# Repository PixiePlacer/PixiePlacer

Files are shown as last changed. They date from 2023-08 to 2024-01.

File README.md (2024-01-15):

# PixiePlacer
Welcome OpenPnP Community to the **PixiePlacer Wiki**!
The PixiePlacer is a **DIY Pick and Place Machine** for SMD Components based around the amazing software **[OpenPnP](https://openpnp.org)**. The machine is designed to be low cost and suited towards mid-scale manufacturing. A big shout out to the developers of [OpenPnP](https://openpnp.org) that keep constantly improving the software.



Something looks wrong? Please [let me know](https://github.com/PixiePlacer/PixiePlacer/issues/new)!

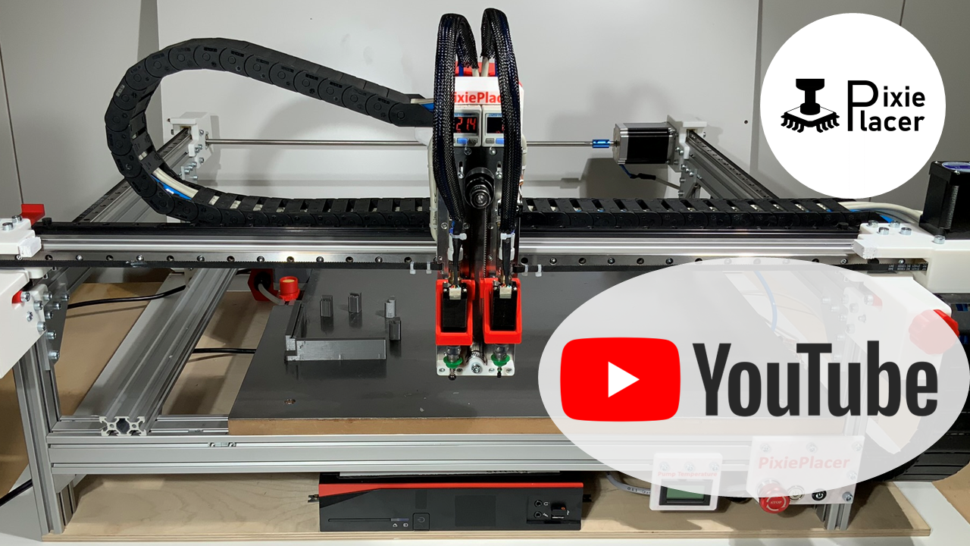
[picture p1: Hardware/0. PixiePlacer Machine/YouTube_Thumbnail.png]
PixiePlacer (https://www.youtube.com/@pixieplacer)


# PixiePlacer Machine
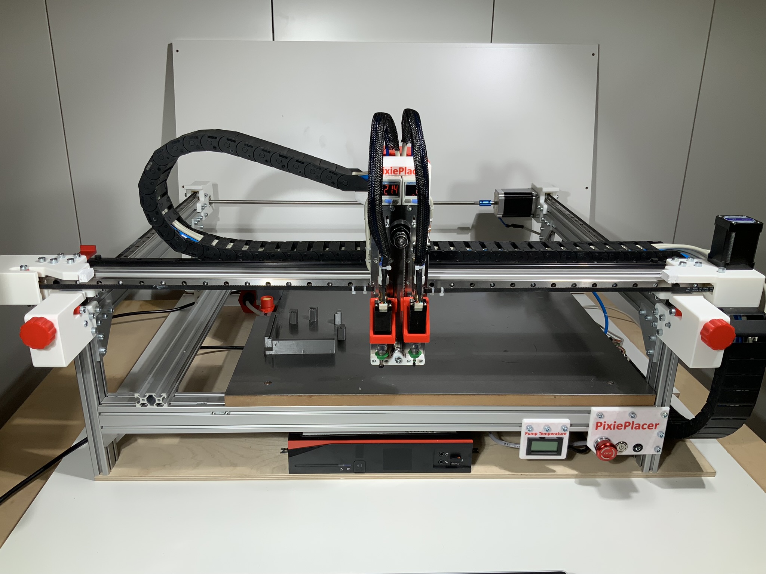
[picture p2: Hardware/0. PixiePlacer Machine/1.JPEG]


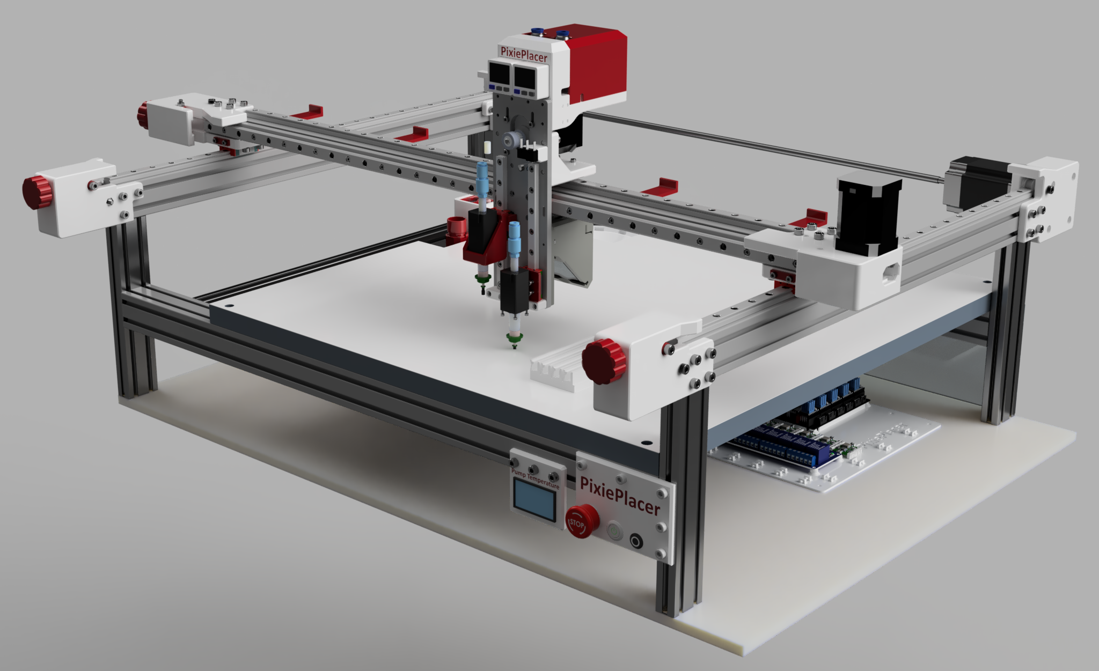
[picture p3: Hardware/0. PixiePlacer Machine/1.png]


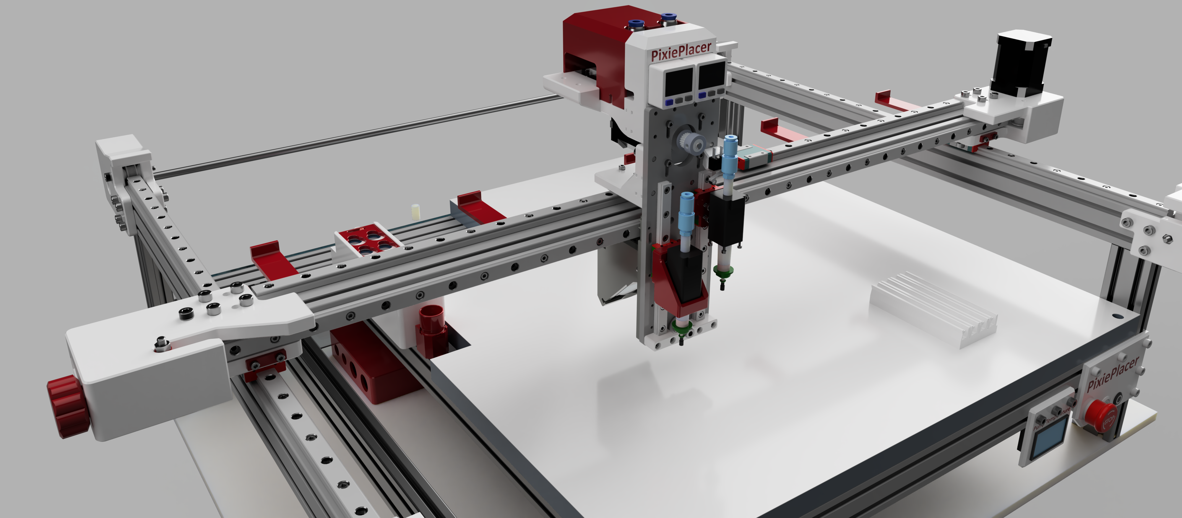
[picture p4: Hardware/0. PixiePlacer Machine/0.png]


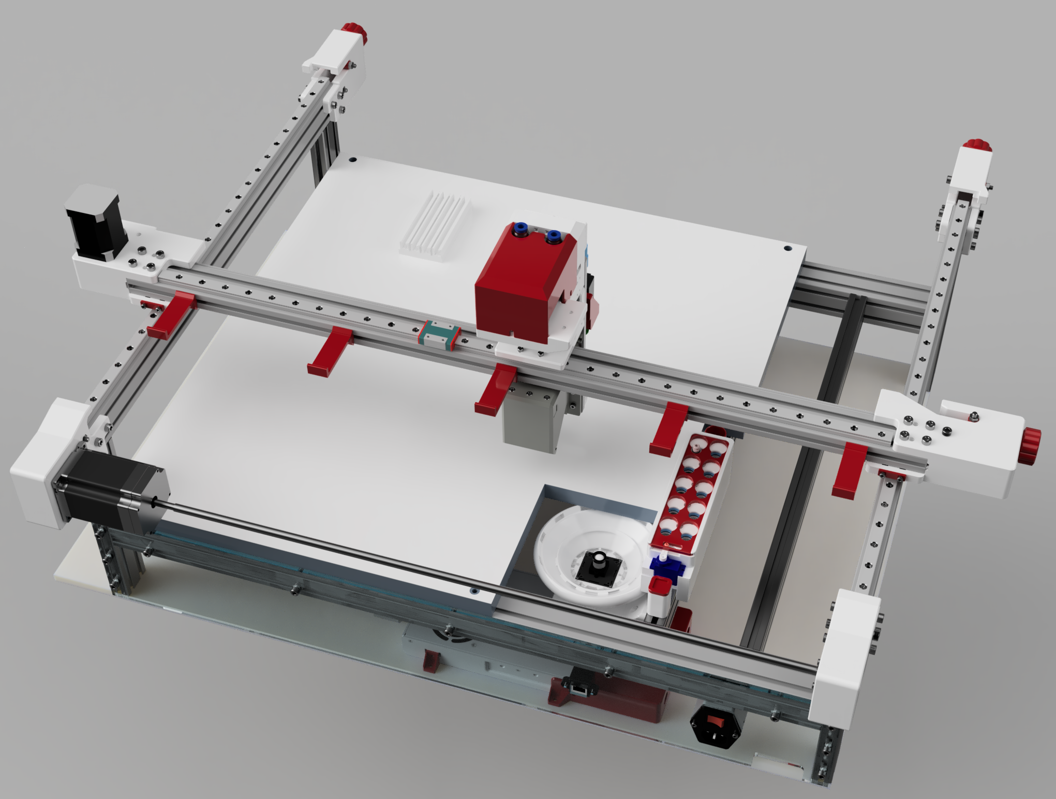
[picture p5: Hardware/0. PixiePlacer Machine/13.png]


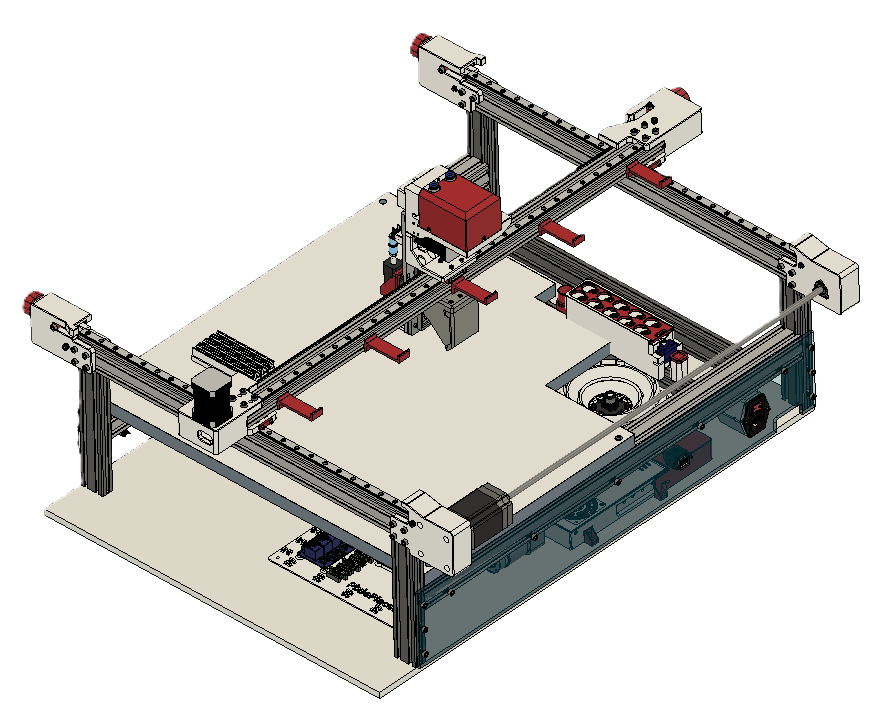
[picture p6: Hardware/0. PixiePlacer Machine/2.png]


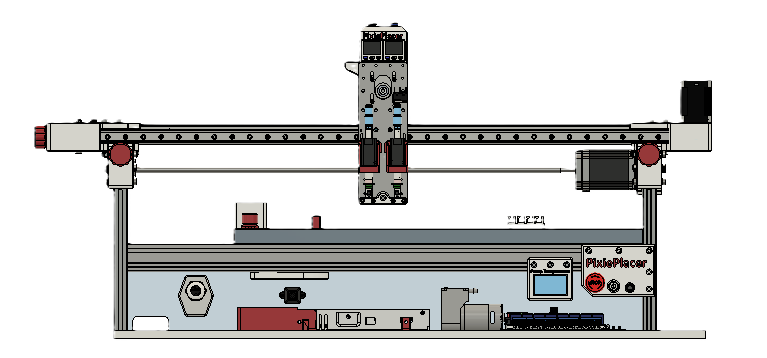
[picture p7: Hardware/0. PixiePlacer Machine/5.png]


***
# Overview
 - [Overview](https://github.com/PixiePlacer/PixiePlacer/wiki/Overview)

# Bill of Materials | BOM
 - [Bill of Materials](https://github.com/PixiePlacer/PixiePlacer/wiki/Bill-of-Materials)
 
# Hardware
 - [Machine Frame](https://github.com/PixiePlacer/PixiePlacer/wiki/Machine-Frame)
 - [Y‐Axis](https://github.com/PixiePlacer/PixiePlacer/wiki/Y%E2%80%90Axis)
 - [X‐Axis](https://github.com/PixiePlacer/PixiePlacer/wiki/X%E2%80%90Axis)
 - [Z‐Axis](https://github.com/PixiePlacer/PixiePlacer/wiki/Z%E2%80%90Axis)
 - Accessories
	- [PCB Holder](https://github.com/PixiePlacer/PixiePlacer/wiki/PCB-Holder)
	- [Down Facing Camera](https://github.com/PixiePlacer/PixiePlacer/wiki/Down-Facing-Camera)
	- [Up Facing Camera](https://github.com/PixiePlacer/PixiePlacer/wiki/Up-Facing-Camera)
	- [Nozzle Changing Station](https://github.com/PixiePlacer/PixiePlacer/wiki/Nozzle-Changing-Station)
	- [Solderpaste Dispensing](https://github.com/PixiePlacer/PixiePlacer/wiki/Solderpaste-Dispensing)

# Electronics
 - [Electronics Diagram](https://github.com/PixiePlacer/PixiePlacer/wiki/Electronics-Diagram)
 - [Pneumatic Diagram](https://github.com/PixiePlacer/PixiePlacer/wiki/Pneumatic-Diagram)

# Software

 - [Marlin ‐ Motion Controller](https://github.com/PixiePlacer/PixiePlacer/wiki/Marlin-%E2%80%90-Motion-Controller)
 - [OpenPnP](https://github.com/PixiePlacer/PixiePlacer/wiki/OpenPnP)

# Component Feeder

 - [Parametric Strip Feeder](https://github.com/PixiePlacer/PixiePlacer/wiki/Parametric-Strip-Feeder)
 - [Automagic PixieFeeder](https://github.com/PixiePlacer/PixiePlacer/wiki/Automagic-PixieFeeder)

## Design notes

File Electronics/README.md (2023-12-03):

# Wiki Electronics

## Electronics Wiring Diagramm
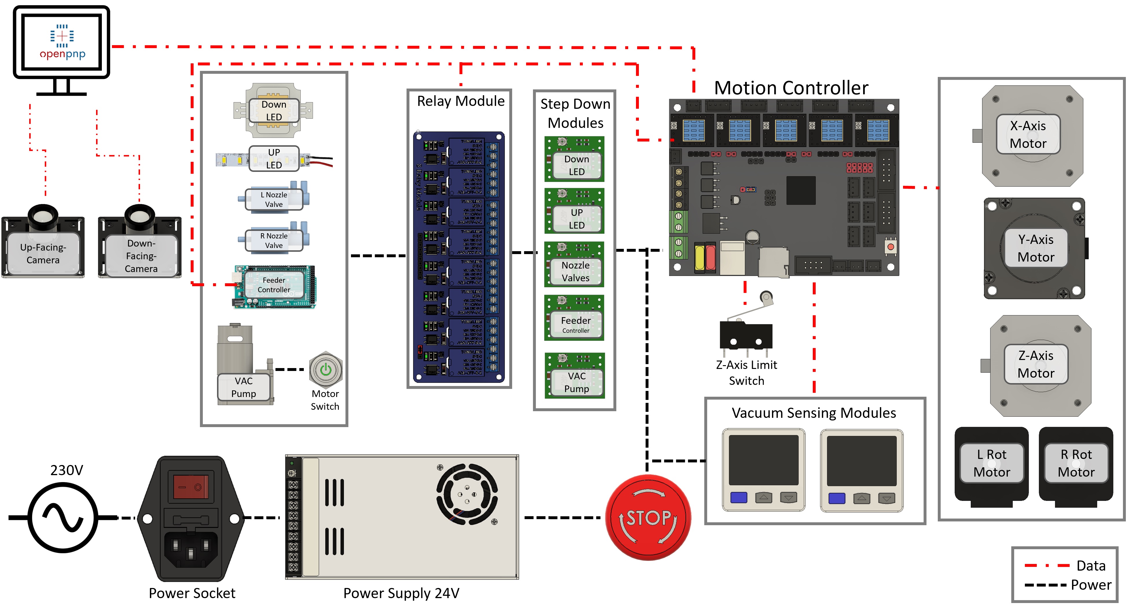
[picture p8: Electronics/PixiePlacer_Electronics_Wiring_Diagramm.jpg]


## Pneuamtic Diagram
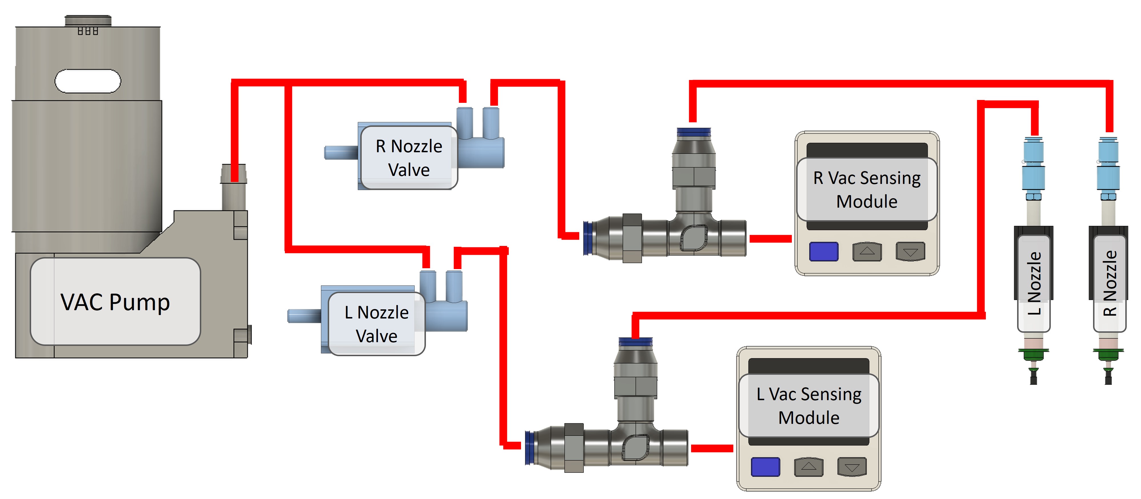
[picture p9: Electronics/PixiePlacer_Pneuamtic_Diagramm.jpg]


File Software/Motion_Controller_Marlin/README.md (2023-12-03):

# [Marlin ‐ Motion Controller Wiki ](https://github.com/PixiePlacer/PixiePlacer/wiki/Marlin-%E2%80%90-Motion-Controller)

**Use the ChangeLog File as a guideline for setting up marlin for your machine.**

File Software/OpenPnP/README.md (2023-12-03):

# [OpenPnP Wiki](https://github.com/PixiePlacer/PixiePlacer/wiki/OpenPnP)

**Use the Machine Setup Files and Driver Setup Files as a guideline for setting up your machine.**

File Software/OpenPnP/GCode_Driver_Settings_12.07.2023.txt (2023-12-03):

++++++++++++  GCode Driver   +++++++++++++
##########  Default  ################

Command Confirm Regrex
	^ok.*

Position Report Regex
	^.*X:(?<X>-?\d+\.\d+) Y:(?<Y>-?\d+\.\d+) Z:(?<Z>-?\d+\.\d+).*

Command Error Regex
	^error.*
	
Connect Command
	G21 ; Set millimeters mode
	G90 ; Set absolute positioning mode
	M82 ; Set absolute mode for extruder
	M42 I M1 P0205 S0; VAC Pump off
	M42 I M1 P0126 S0; LED Top on
	M42 I M1 P0010 S255; LED Bottom off
	M42 I M1 P0100 S255; Air Nozzle 1 off
	M42 I M1 P0125 S255; Air Nozzle 2 off

Disable Command
	M84 ; stepper motor off
	M42 I M1 P0205 S0; VAC off
	M42 I M1 P0205 S0; VAC Pump off
	M42 I M1 P0126 S255; LED Top off
	M42 I M1 P0010 S255; LED Bottom off
	M42 I M1 P0100 S255; Air Nozzle 1 off
	M42 I M1 P0125 S255; Air Nozzle 2 off
	
Home Command
	G28 Z;
	G28 Z;
	G0 Z0 F1000;
	G28 XY
	G0 X0 Y0 Z0 F10000;
	T0 S1;
	G92 E0;
	T1 S1;
	G92 E0;
	M42 I M1 P0205 S0; VAC Pump off
	M42 I M1 P0126 S0; LED Top on
	M42 I M1 P0010 S255; LED Bottom off
	M42 I M1 P0100 S255; Air Nozzle 1 off
	M42 I M1 P0125 S255; Air Nozzle 2 off
	
## Pump On Command
	M42 I M1 P0205 S255; VAC on
	
## Pump Off Command
	M42 I M1 P0205 S0;

Get Position Command
	M114 ; get position
	
Move to Command
	G0 {X:X%.4f} {Y:Y%.4f} {Z:Z%.4f} {Rotation:E%.4f} F{FeedRate:%.0f		
				
Move to Complete Command
	M400 ; Wait for moves to complete before returning

In machine.xml

supporting-pre-move="true" using-letter-variables="false"

<pre-move-command><![CDATA[
					T0S1
					G92E{Coordinate:%.4f}
				]]></pre-move-command>

<pre-move-command><![CDATA[
					T1S1
					G92E{Coordinate:%.4f}
				]]></pre-move-command>		
	
NEW #############   H1 VAC PUMP   #############
Actuate Boolean Command
		{True:M42 I M1 P0205 S255}{False:M42 I M1 P0205 S0}

Not Existing ##############   H1 N1   #####################
Place Command
	M42 I M1 P0100 S255; Air Nozzle 1
	G4 P250;

Not existing ##############   H1 N2   #####################
Place Command
	M42 I M1 P0125 S255; Air Nozzle 2
	G4 P250;

#############   H1 N1_Vac   #############
Actuate Boolean Command
	{True:M42 I M1 P0100 S0}{False:M42 I M1 P0100 S255}
	M42 I M1 P0205 S255; VAC on

#############   H1 N2_Vac   #############
Actuate Boolean Command
	{True:M42 I M1 P0125 S0}{False:M42 I M1 P0125 S255}
	M42 I M1 P0205 S255; VAC on
	
#############   H1 Solder Dispenser   #############
Actuate Boolean Command
	{True:M106 S255}{False:M106 S0}
	
#############   H1 Top Light   #############
Actuate Boolean Command
	{True:M42 I M1 P0010 S255}{False:M42 I M1 P0010 S0}
	{True:M42 I M1 P0126 S0}{False:M42 I M1 P0126 S255}

#############   Bottom Light   #############
Actuate Boolean Command
	{True:M42 I M1 P0010 S0}{False:M42 I M1 P0010 S255}
	{True:M42 I M1 P0126 S255}{False:M42 I M1 P0126 S0}

#############   Shot Solder Dispenser   #############
Actuate Boolean Command
	M106 S255				; On Solder Paste Dispenser
	G4 P500 				; Wait 50ms
	M106 S0					; Off Solder Paste Dispenser

#############   Pneumatic Advance   #############
Actuate Boolean Command
	M106 S0
	G4 P300
	M106 S255

#############   Pneumatic Post Pickup   #############
Actuate Boolean Command

++++++++++++++ Feeder Controller   ++++++++++++++++

##########  Default  ################

Command Confirm Regrex
	^ok.*
	
Command Error Regex
	^error.*	
	
Connect Command
	M610 S1 ; enable feeder

Enable Command
	M610 S1 ; enable feeder

Disable Command
	M610 S0 ; disable feeder
	
#############   Auto Feeder_4mm Advance   #############
Actuate Double Command
	M600 N{IntegerValue} F4
	
#############   Auto Feeder_8mm Advance   #############
Actuate Double Command
	M600 N{IntegerValue} F8

#############   Auto Feeder_12mm Advance   #############
Actuate Double Command
	M600 N{IntegerValue} F12

#############   Auto Feeder_PostPickup   #############
Actuate Double Command
	M601 N{IntegerValue}

#############   Auto Feeder_Enable   #############
Actuate Boolean Command
	M610 S{True:1}{False:0}

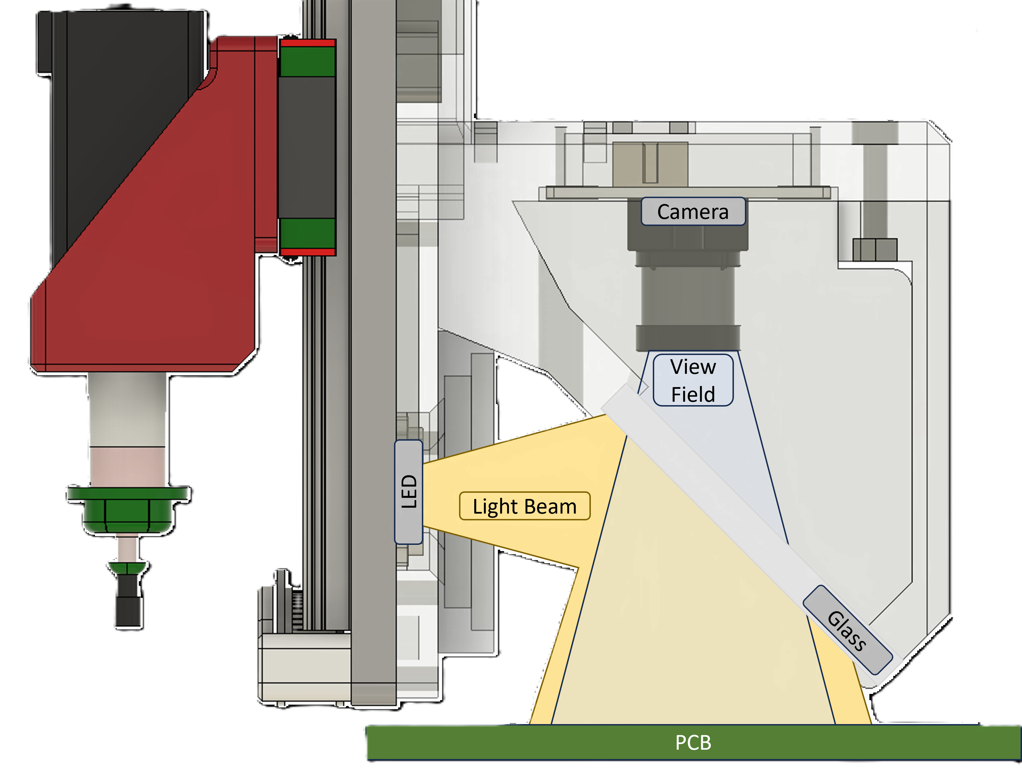
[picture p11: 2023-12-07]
Hardware/5. Accessories/Down-Facing-Camera/Beam-Splitter_Side-View.png

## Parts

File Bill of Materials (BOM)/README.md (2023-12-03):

# Bill of Materials PixiePlacer Table
[Bill of Materials PixiePlacer Table](https://docs.google.com/spreadsheets/d/1CWFQ7bArdYDCNkc-MHFDlqN6pdHpugMOtVum4YUrMk8/edit?usp=sharing)

***

# [Wiki Bill of Materials | BOM](https://github.com/PixiePlacer/PixiePlacer/wiki/Bill-of-Materials)

PixiePlacer (https://www.youtube.com/@pixieplacer)

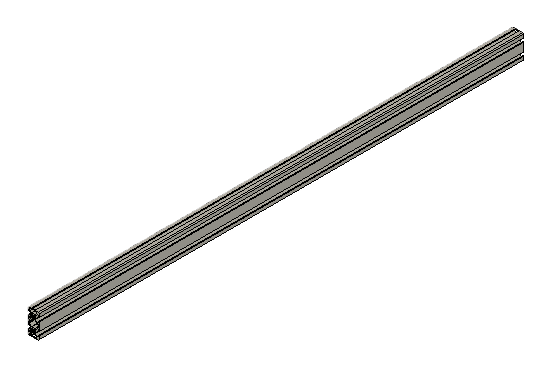
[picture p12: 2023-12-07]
Bill of Materials (BOM)/Parts/3. X-Axis/Alu_Extrusion_X-Axis_798mm.png

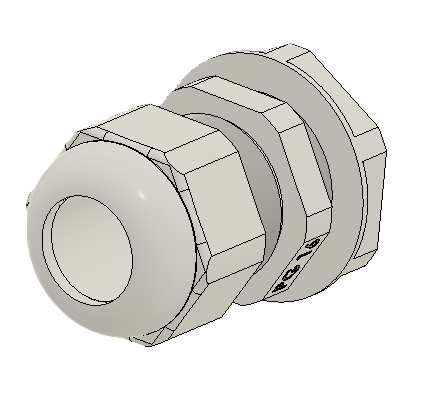
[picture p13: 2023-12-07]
Bill of Materials (BOM)/Parts/1. Machine Frame/Back_Panel/Cable_Gland_PG16.png

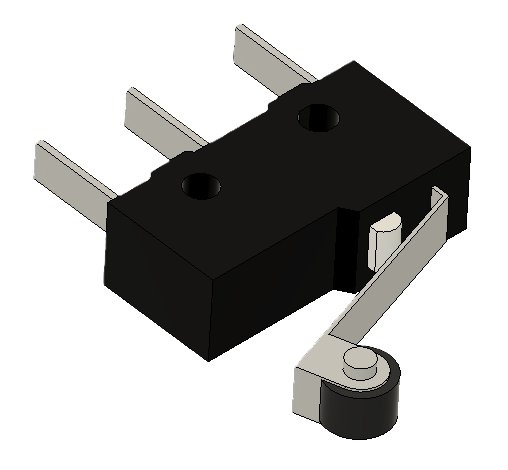
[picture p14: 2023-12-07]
Bill of Materials (BOM)/Parts/4. Z-Axis/Z-Axis_Limit_Switch.png

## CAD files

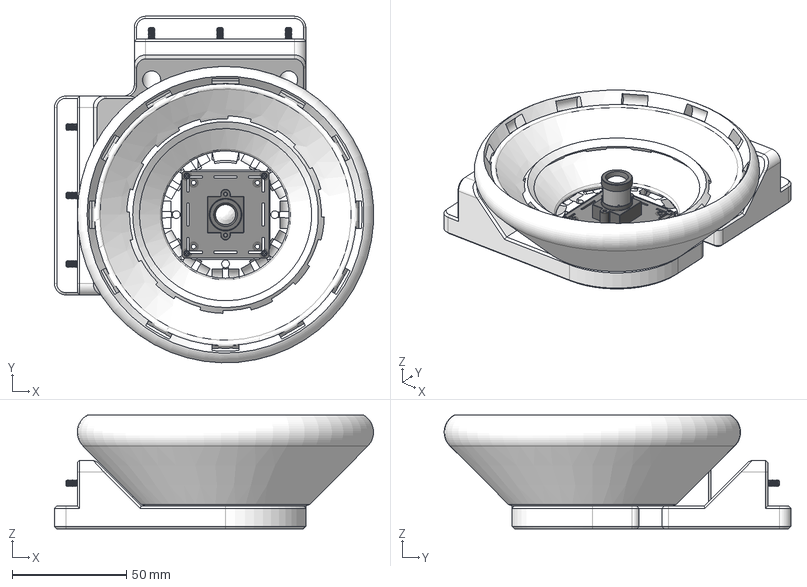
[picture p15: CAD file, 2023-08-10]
Hardware/5. Accessories/Up-Camera/Up_Camera_Assembly.step
139.9 x 152.0 x 49.8 mm
USB_Camera
Socket_Cap_Screw_M3x16mm x 6
99461A913_Phillips Rounded Head Thread-Forming Screws x 4

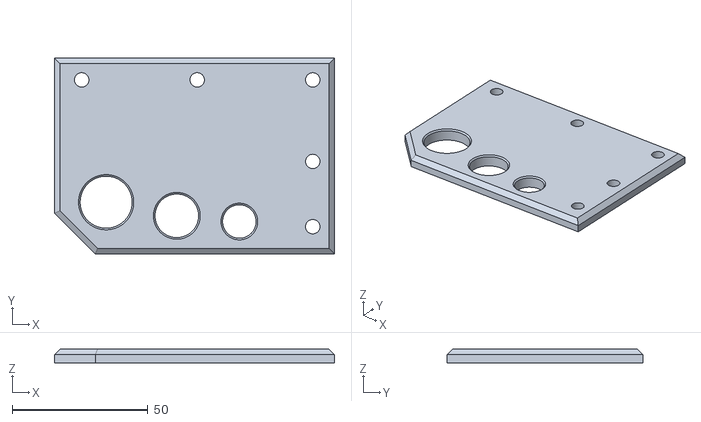
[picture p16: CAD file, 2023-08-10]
Hardware/1. Machine Frame/STL Files/Front_Panel.stl
103.0 x 72.0 x 5.00

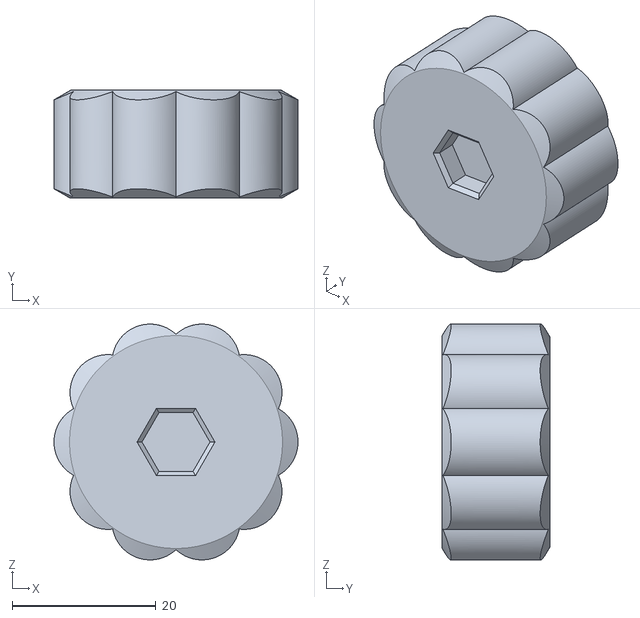
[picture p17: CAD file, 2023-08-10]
Hardware/2. Y-Axis/STL Files/Star_Knob_Base.stl
34.0 x 15.0 x 32.9

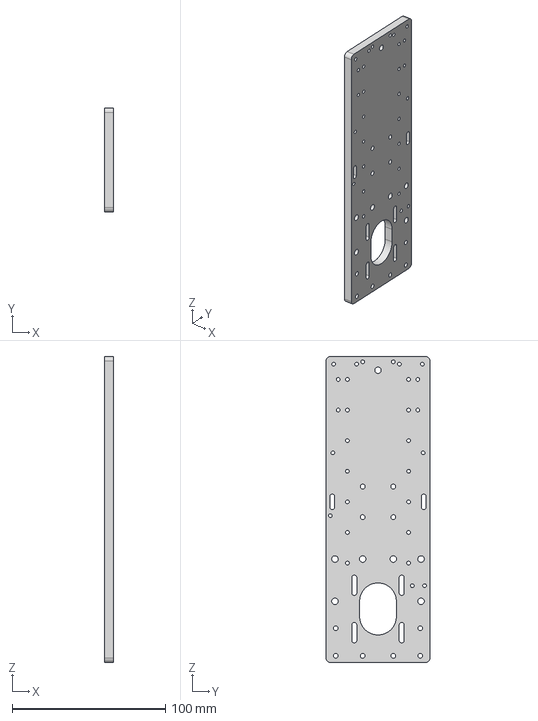
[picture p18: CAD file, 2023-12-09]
Hardware/4. Z-Axis/Manufacturing Files Z-Axis_Mounting_Plate/Z-Axis_Mounting_Plate.step
6.00 x 68.0 x 200.0 mm

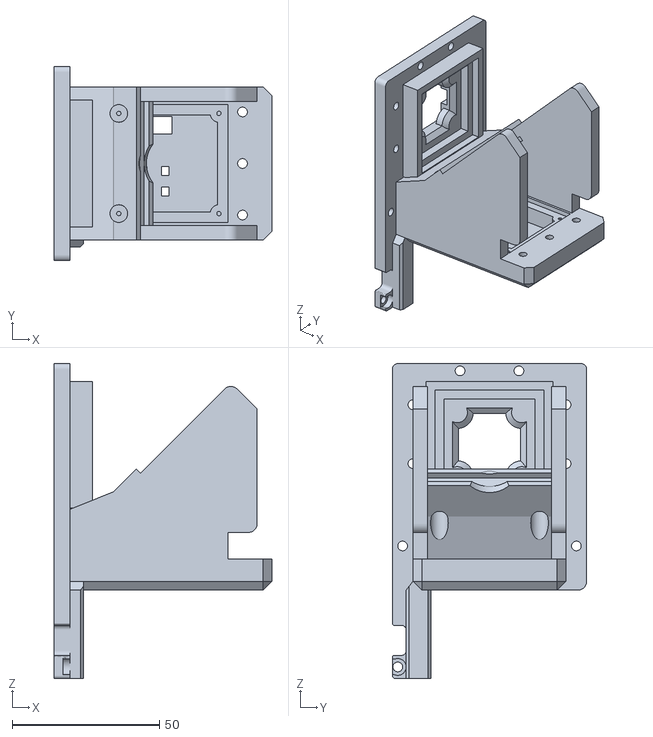
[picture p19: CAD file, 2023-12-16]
Hardware/4. Z-Axis/STL Files/Down-Camera/Beamsplitter_Base.stl
74.0 x 66.0 x 107.0

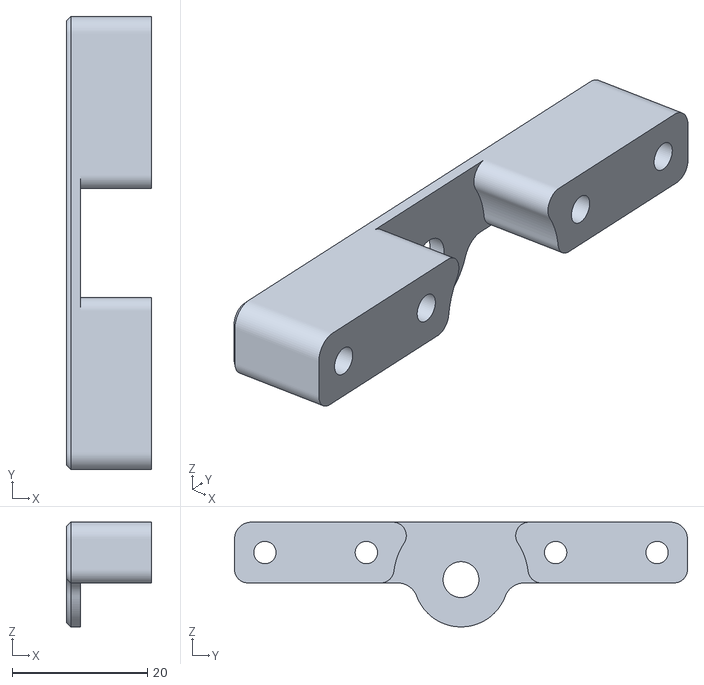
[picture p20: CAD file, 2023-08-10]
Hardware/4. Z-Axis/STL Files/End_Stop_Linear_Rail.stl
12.5 x 67.0 x 15.5

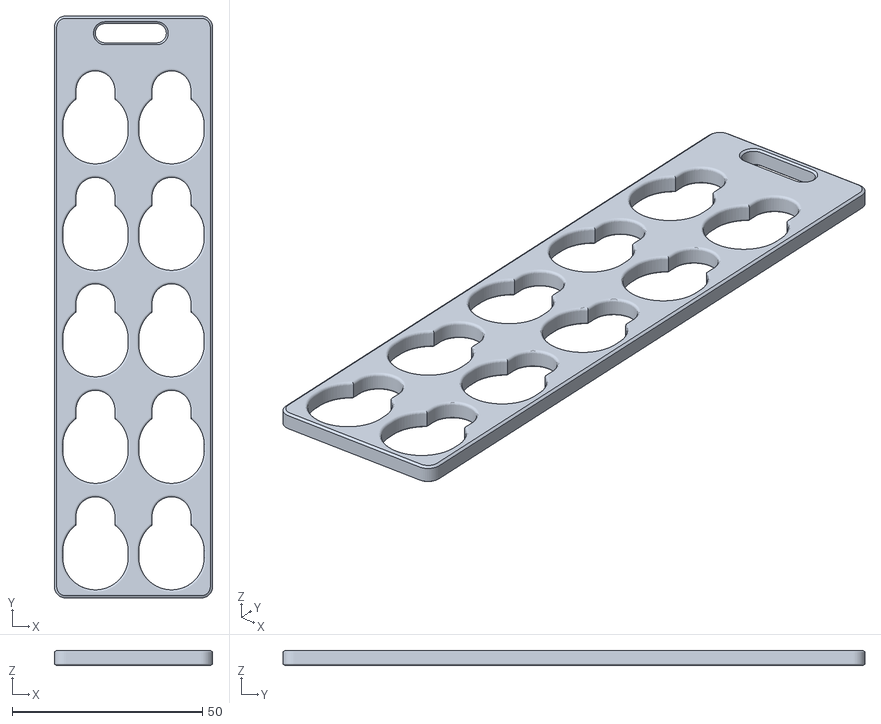
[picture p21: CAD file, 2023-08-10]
Hardware/5. Accessories/Nozzle_Changer/Nozzler_Changer_Slider.stl
41.6 x 153.0 x 4.00

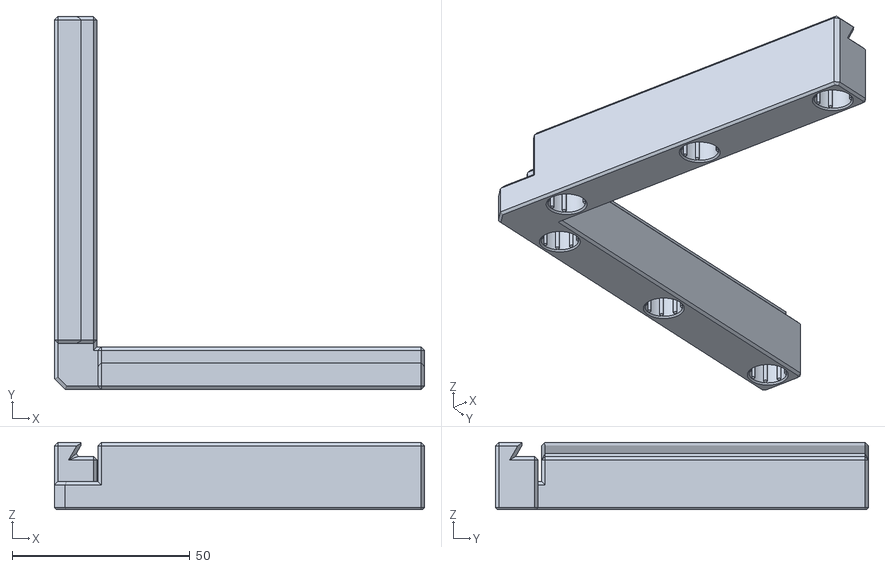
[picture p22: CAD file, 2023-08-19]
Hardware/5. Accessories/PCB_Mount/PCB_Mount_Square.stl
104.2 x 105.0 x 19.0

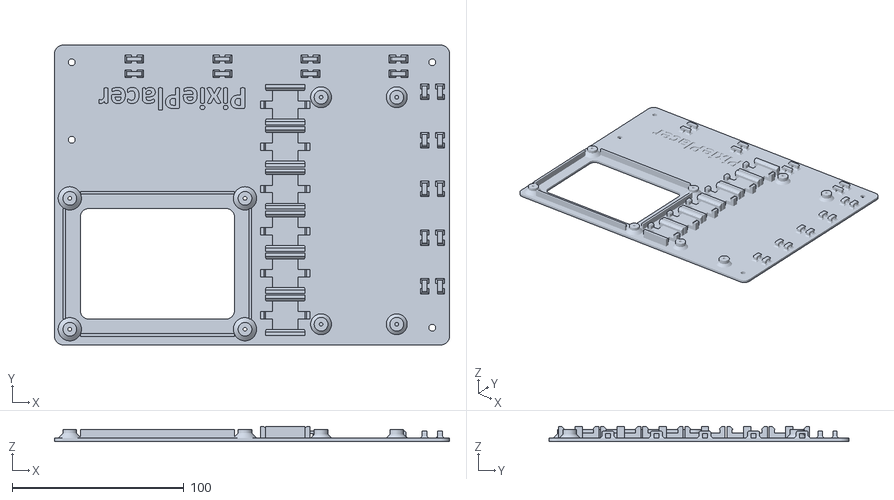
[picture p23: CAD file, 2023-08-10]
Hardware/5. Accessories/STL Files/Electronics_Mounting_Plate.stl
229.7 x 174.3 x 8.60

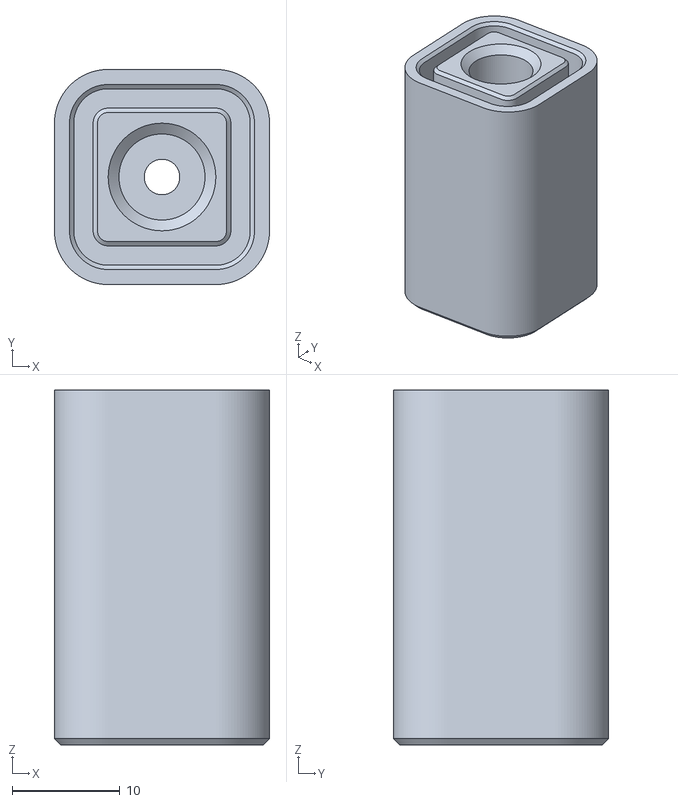
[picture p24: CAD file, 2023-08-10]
Hardware/5. Accessories/STL Files/Homing_Fiducial/Homing_Fiducial_Mount_Base.stl
20.0 x 20.0 x 33.0

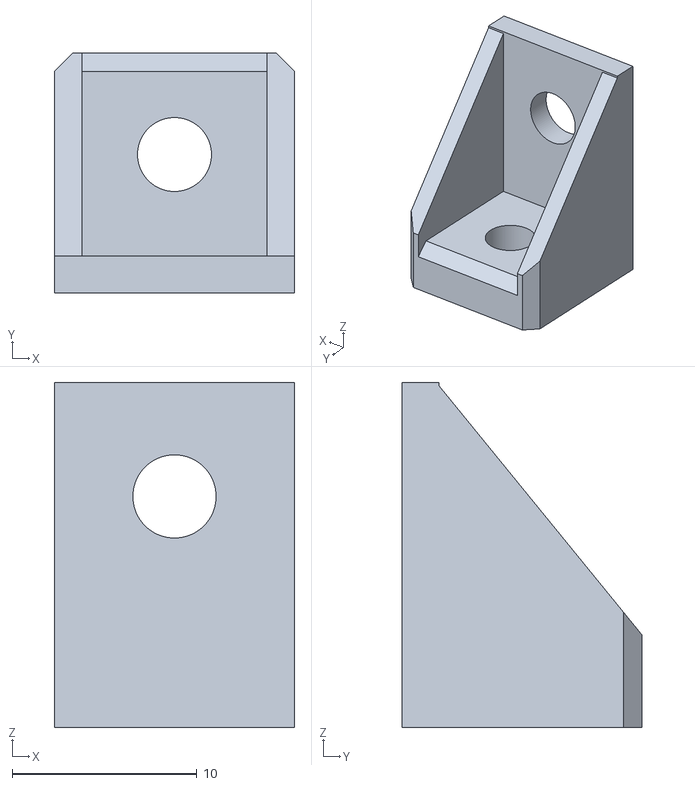
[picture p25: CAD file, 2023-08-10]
Hardware/5. Accessories/STL Files/Power_Supply/Power_Supply_Mount_1.stl
13.0 x 13.0 x 18.7

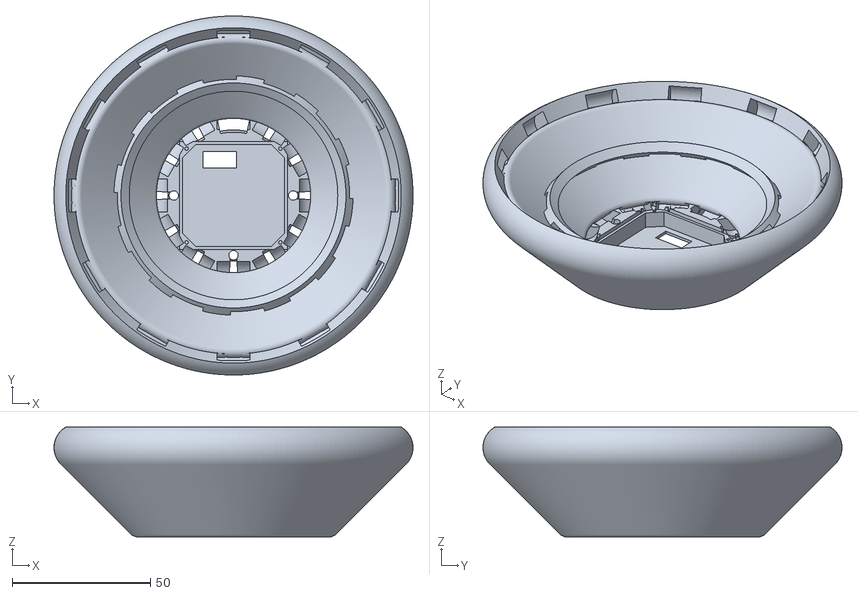
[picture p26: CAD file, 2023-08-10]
Hardware/5. Accessories/Up-Camera/Light_Cone_Up_Camera.stl
130.0 x 130.0 x 39.8

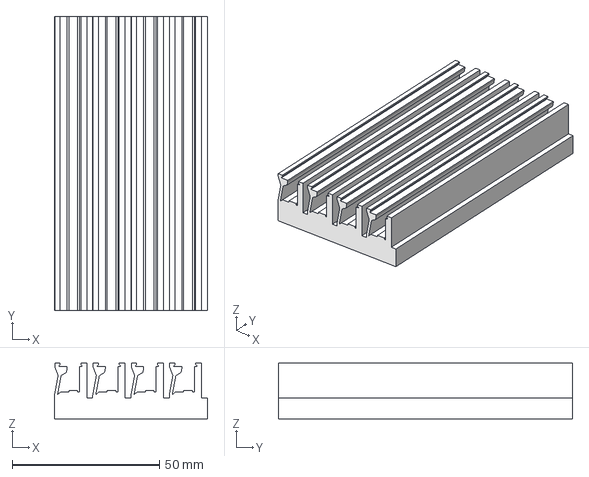
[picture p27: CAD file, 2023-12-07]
Hardware/6. Parametric Strip Feeder/CAD Files/Parametric_Strip_Feeder.step
52.0 x 100.0 x 18.9 mm

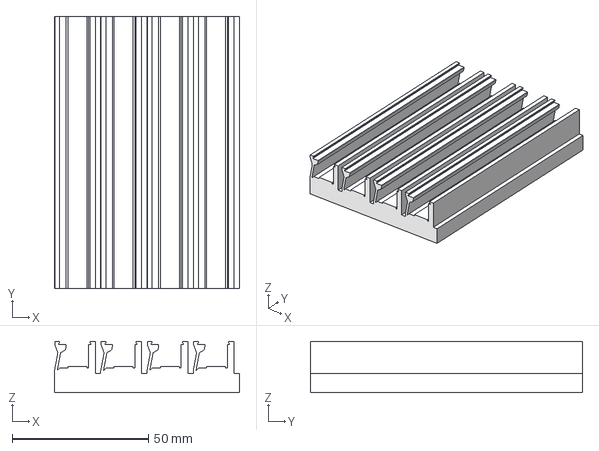
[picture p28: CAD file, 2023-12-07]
Hardware/6. Parametric Strip Feeder/CAD Files/Strip_Feeder_12mm/Strip_Feeder_12mm.step
68.0 x 100.0 x 18.9 mm

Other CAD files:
Hardware/6. Parametric Strip Feeder/CAD Files/Strip_Feeder_16mm/Strip_Feeder_16mm.step
Hardware/6. Parametric Strip Feeder/CAD Files/Strip_Feeder_24mm/Strip_Feeder_24mm.step
Hardware/1. Machine Frame/STL Files/Power_Socket_Cover.stl
Hardware/1. Machine Frame/STL Files/Temperatur_Gauge_Panel.stl
Hardware/2. Y-Axis/STL Files/Left_Back_Mounting_Plate_Y-Axis.stl
Hardware/2. Y-Axis/STL Files/Left_Front_Mounting_Plate_Y-Axis.stl
Hardware/2. Y-Axis/STL Files/Right_Back_Mounting_Plate_Y-Axis.stl
Hardware/2. Y-Axis/STL Files/Right_Front_Mounting_Plate_Y-Axis.stl
Hardware/2. Y-Axis/STL Files/Star_Knob_Cover.stl
Hardware/2. Y-Axis/STL Files/Tension_Slider.stl
Hardware/2. Y-Axis/STL Files/Wedge.stl
Hardware/3. X-Axis/STL Files/Left_Mounting_Plate_X-Axis.stl
Hardware/3. X-Axis/STL Files/Right_Mounting_Plate_X-Axis.stl
Hardware/3. X-Axis/STL Files/Star_Knob_Cover.stl
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

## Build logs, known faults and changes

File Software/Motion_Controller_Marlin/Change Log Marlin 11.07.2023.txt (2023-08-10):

Change Log 11.07.2023

Install and Open VSCode
Install PlatformIO Extension
Open the Marlin Folder in VSCode
Make Sure that the Marlin Folder is not in a File Drectory (Path) that contains any Spaces or Special Caracters -> This will safe you a lot of problems

--------------
Open "Platformio.ino" from the Menu left
	Change
		default_envs = mega2560
		TO
		default_envs = LPC1769
When Pressing the "Build Button" on the bottom the Compiled code is in the .pio folder under builds.

Inorder to flash the Firmware on the Board. the builded hex file needs to be copied to a micro SD. Insert the microSD card into the board and reboot it. It will copy over the new firmware.

Afterwards the EPROM needs to be updated!

--------------------------------------------------------------------------------------------------------------------------------
Marlin-> src -> Pins -> LPC1769 -> Skr 1.4

--------------------------------------------------------------------------------------------------------------------------------
Marlin-> Configuration.h

§§§	Change:	§§§§
#define STRING_CONFIG_H_AUTHOR "PixiePlacer"
#ifndef MOTHERBOARD
  #define MOTHERBOARD BOARD_BTT_SKR_V1_4_TURBO
#endif

§§§	Change: §§§§
#define SERIAL_PORT -1

§§§	Change: §§§§
#define BAUDRATE 115200

§§§	Uncomment and Change: §§§§
#define SERIAL_PORT_2 0
#define BAUDRATE_2 115200   // Enable to override BAUDRATE

§§§	Uncomment and Change: §§§§
#define CUSTOM_MACHINE_NAME "PixiePlacer 11.07.2023"	//get with M115

§§§	Uncomment and Change: §§§§
#define X_DRIVER_TYPE  TMC5160
#define Y_DRIVER_TYPE  TMC5160
#define Z_DRIVER_TYPE  TMC5160
#define E0_DRIVER_TYPE TMC2208
#define E1_DRIVER_TYPE TMC2208

§§§	Change:	§§§§
#define EXTRUDERS 2

§§§	Change:	§§§§
#define TEMP_SENSOR_0 998
#define TEMP_SENSOR_1 998

§§§	Comment: §§§§
//#define PIDTEMPBED
//#define PREVENT_COLD_EXTRUSION
//#define EXTRUDE_MINTEMP 170
//#define PREVENT_LENGTHY_EXTRUDE
//#define EXTRUDE_MAXLENGTH 200

//#define THERMAL_PROTECTION_HOTENDS
//#define THERMAL_PROTECTION_BED
//#define THERMAL_PROTECTION_CHAMBER
//#define THERMAL_PROTECTION_COOLER

§§§	Uncomment and Change: §§§§
#define USE_XMIN_PLUG
#define USE_YMIN_PLUG
#define USE_ZMIN_PLUG
//#define USE_XMAX_PLUG
//#define USE_YMAX_PLUG
//#define USE_ZMAX_PLUG

§§§	Change: §§§§
#define X_MIN_ENDSTOP_INVERTING true
#define Y_MIN_ENDSTOP_INVERTING true
#define Z_MIN_ENDSTOP_INVERTING true
#define X_MAX_ENDSTOP_INVERTING true
#define Y_MAX_ENDSTOP_INVERTING true
#define Z_MAX_ENDSTOP_INVERTING true
#define Z_MIN_PROBE_ENDSTOP_INVERTING true

§§§	Uncomment: §§§§
#define ENDSTOPPULLUP_XMIN
#define ENDSTOPPULLUP_YMIN

§§§	Uncomment and Change: §§§§
#define DEFAULT_AXIS_STEPS_PER_UNIT   { 10,   10,  80, 8.888}
#define DEFAULT_MAX_FEEDRATE          { 200, 180, 100,  1000}
#define DEFAULT_MAX_ACCELERATION      { 500, 500, 1000, 1000}

#define DEFAULT_ACCELERATION          3000
#define DEFAULT_RETRACT_ACCELERATION  3000
#define DEFAULT_TRAVEL_ACCELERATION   3000
#define CLASSIC_JERK
#define DEFAULT_XJERK 0
#define DEFAULT_YJERK 0
#define DEFAULT_ZJERK 0
#define DEFAULT_EJERK 0

§§§	Comment: §§§§
//#define Z_MIN_PROBE_USES_Z_MIN_ENDSTOP_PIN

§§§	Change: §§§§
#define NOZZLE_TO_PROBE_OFFSET { 0, 0, 0 }
#define PROBING_MARGIN 100				
#define XY_PROBE_FEEDRATE 50			
#define Z_PROBE_FEEDRATE_FAST 50		
#define Z_PROBE_FEEDRATE_SLOW 10	

§§§	Uncomment and Change: §§§§
#define MULTIPLE_PROBING 2				

§§§	Change: §§§§
#define Z_CLEARANCE_DEPLOY_PROBE   10	
#define Z_CLEARANCE_BETWEEN_PROBES  5	
#define Z_CLEARANCE_MULTI_PROBE     5	

#define Z_PROBE_LOW_POINT          -83
#define Z_PROBE_OFFSET_RANGE_MIN -82
#define Z_PROBE_OFFSET_RANGE_MAX 160

§§§	Comment: §§§§
//#define DISABLE_E false
//#define DISABLE_INACTIVE_EXTRUDER

§§§	Change: §§§§
#define INVERT_X_DIR true
#define INVERT_Y_DIR true
#define INVERT_Z_DIR true

#define X_BED_SIZE 610
#define Y_BED_SIZE 527

#define Z_MAX_POS 80

§§§	Comment: §§§§
//#define MIN_SOFTWARE_ENDSTOP_Z
//#define MAX_SOFTWARE_ENDSTOP_Z

§§§	Change: §§§§
#define HOMING_FEEDRATE_MM_M { 4000, 4000, 4000 }

§§§	Uncomment: §§§§
#define EEPROM_SETTINGS

§§§	Comment: §§§§
//#define PRINTJOB_TIMER_AUTOSTART

#define SERVO_DELAY { 300,300 }
#define NUM_SERVOS 2
#define DEACTIVATE_SERVOS_AFTER_MOVE

#define SERVO0_PIN                         P2_00
#define SERVO1_PIN                         P2_00

--------------------------------------------------------------------------------------------------------------------------------

Marlin-> Configuration_adv.h

§§§	Comment: §§§§
//#define AUTOTEMP

§§§	Change: §§§§
#define HOMING_BUMP_MM      { 0, 0, 2 }

#define DEFAULT_STEPPER_DEACTIVE_TIME 0
#define DISABLE_INACTIVE_X false
#define DISABLE_INACTIVE_Y false
#define DISABLE_INACTIVE_Z false
#define DISABLE_INACTIVE_E false

§§§	Uncomment and Change: §§§§
#define SAVED_POSITIONS 2

§§§	Comment: §§§§
//#define SLOWDOWN

§§§	Change: §§§§
#define MIN_STEPS_PER_SEGMENT 1

//VREF = I x 8 x Rsense
#define X_CURRENT       1500 //2.1A Motor (Max 1600)
#define X_MICROSTEPS    8
#define X_RSENSE        0.075
#define Y_CURRENT       2500 //4A Motor  (Max 3100)
#define Y_MICROSTEPS    8
#define Y_RSENSE        0.075
#define Z_CURRENT       1500 //2.1A Motor
#define Z_RSENSE        0.075
#define E0_CURRENT      600
#define E1_CURRENT      600

§§§	Uncomment: §§§§
#define TMC_USE_SW_SPI

§§§	Change: §§§§
#define E0_SLAVE_ADDRESS 0
#define E1_SLAVE_ADDRESS 0

#define CHOPPER_TIMING CHOPPER_DEFAULT_24V

§§§	Uncomment: §§§§
#define SENSORLESS_HOMING  

§§§	Change: §§§§
#define X_STALL_SENSITIVITY  5
#define Y_STALL_SENSITIVITY  7

§§§	Uncomment: §§§§
#define MONITOR_DRIVER_STATUS
#define TMC_DEBUG				//could lead to memory overflow

§§§	Uncomment: §§§§
#define CNC_COORDINATE_SYSTEMS

§§§	Comment: §§§§
//#define AUTO_REPORT_TEMPERATURES
//#define EXTENDED_CAPABILITIES_REPORT

§§§	Change: §§§§
#define STARTUP_COMMANDS "M119" //Startup commands

§§§	Uncomment: §§§§
#define GCODE_MACROS	// M810-M819 to define and run G-code macros.			
#define DIRECT_PIN_CONTROL
#define PINS_DEBUGGING

***** Interesting:
//#define CUSTOM_USER_BUTTONS		// Testing *****	
#define SENSORLESS_HOMING

Fragen: SPW Working?
E0_SLAVE_ADDRESS ??
#define HYBRID_THRESHOLD // Active switching from quite to load // Testing *****

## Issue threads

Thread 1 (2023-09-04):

Nozzle Changer

AzureOz, 2023-09-04:
Great project, thank you for sharing it.  I know you are just starting to post info on various parts of the project and I look forward to your updates.
Are you able to add any info on the Juki Nozzle Changer?
Any setup, connection, configuration and programming needed for the changer operation and it's servo drive.
A video of it changing bits would be wonderful.

slaesh, 2023-09-28:
great stuff. recently saw this [video here](https://www.youtube.com/watch?v=kQ9cqHOH0Uc) from @Mike-Menci. looks similar, maybe you guys can connect and build one awesome instead of two great ones :)

Mike-Menci, 2023-09-28:
Salaesh - Similar to ??

Mike-Menci, 2023-09-28:
Oh I see what you mean...

PixiePlacer, 2023-10-22:
Yes the design is based on the work of @Mike-Menci. Credits are now given [here](https://github.com/PixiePlacer/PixiePlacer/wiki/Nozzle-Changing-Station). I would love to colaborate on the desin. Mike does amazing work, especially his work on the Component Feeders.

PixiePlacer, 2023-12-03:
I am using this head: [Link](https://www.aliexpress.us/item/3256801583850616.html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)

PixiePlacer, 2023-12-03:
@Mike-Menci I love your feeder designs a lot and I can't wait to see your progress in the future. DM me on Discord if you want ;)

Closed 2023-12-03.

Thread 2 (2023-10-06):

Clarify the Vaccuum sensor part number.

edcasati, 2023-10-06:
I am having trouble locating the Vaccuum sensor.
The P/N that you provide is "NC3RR-96FJ4-KP6JP-MGM8W-VH66Y" but can't be found.

PixiePlacer, 2023-10-06:
Sorry, the part number is: ZSE30A-01-N-L
Glad I could help you :)

Am 06.10.2023 um 17:28 schrieb Edward Casati ***@***.***>:

I am having trouble locating the Vaccuum sensor.
The P/N that you provide is "NC3RR-96FJ4-KP6JP-MGM8W-VH66Y" but can't be found.

—
Reply to this email directly, view it on GitHub<https://github.com/PixiePlacer/PixiePlacer/issues/2>, or unsubscribe<https://github.com/notifications/unsubscribe-auth/A3SAKN7RK3MLMGUDLGEBF2DX566JRAVCNFSM6AAAAAA5VORAWOVHI2DSMVQWIX3LMV43ASLTON2WKOZRHEZDSNRYGA4DENQ>.
You are receiving this because you are subscribed to this thread.Message ID: ***@***.***>

Closed 2023-10-06.

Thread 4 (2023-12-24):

Typo in `Pneuamtic Diagram` Wiki title

HammyHavoc, 2023-12-24:
Should be `Pneumatic Diagram`. :- )

I'd edit it myself, but looks like GitHub is a little quirky in regards to wikis and permissions as forking doesn't seem to copy the wiki to be able to do pull requests.

Closed 2024-01-15.

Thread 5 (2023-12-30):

Which Juki Nozzle?

austinchambers, 2023-12-30:
Hello! I'm going through the BOM to create my shopping list, and I'm stuck on the selection of the Juki Nozzle. It doesn't seem to specify which to purchase. Is it a 504 or 503?

Also, let me know if you'd like me to share a copy of my shopping list. I'm trying to coalesce, price, and simplify the BOM as much as possible to make it easier for folks to purchase parts. And if there's a discord to join for this project, please let me know!

Thanks!

austinchambers, 2023-12-31:
So it looks like the juki nozzles are selected based on your application. So it's not a fixed size for the pixieplacer, but based rather on what components you are placing.

There's a table in this location: http://avipre.com/products/smt&tht/juki//Juki%20-%20Nozzle%20Catalogue-Rev-C3.pdf

So, for example, since my smallest parts are 0805 and my largest is ~6mmx6mm, then I've got to go with the 504 nozzle and the 506 nozzle

Closed 2023-12-31.

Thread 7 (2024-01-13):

Wiring detail regarding relays and stepping down voltage.

Jai-R1gby, 2024-01-13:
Hi there,

Was wondering if it would be possible to get some greater detail regarding the wiring setup of the relays and how they connect to the main board. Once they are connected to the main board how is this then addressed by Marlin.

Many thanks.

PixiePlacer, 2024-01-15:
Hey,
see this [link ](https://github.com/PixiePlacer/PixiePlacer/wiki/Marlin-%E2%80%90-Motion-Controller)for the detailed wiring.

Closed 2024-01-15.

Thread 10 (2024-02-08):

can one contribute?

Contomo, 2024-02-08:
Sorry im kinda new to github so im not sure issues is the right place but, i built the pixiplacer using 15mm rails instead of the 12mm ones, i redesigned some parts and designed fitting optical endstops, a mount for the BTT octopus V1 pro a cable chain with adapters etc etc
is there a place to post/share those?

PixiePlacer, 2024-02-09:
Hello @Contomo,
thats amazing that you have build the machine. I would love to see some pictures of the machine if possible.
Sure I can upload the files if you want. Just send me an Email to: PixiePlacer@outlook.com or DM on Discord.
PixiePlacer

Closed 2024-02-11.

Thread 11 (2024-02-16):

solder paste dispenser

AndreyFly007, 2024-02-16:
Спасибо, что поделились проектом.
На какой стадии дозатор паяльной пасты? Проект будет продолжаться?

Thanks for sharing the project.
At what stage is the solder paste dispenser? Will the project continue?

PixiePlacer, 2024-02-27:
Hey,
I am currently not working on the solder paste dispenser. I woudn't bet on me continuing the development of the solder paste dispenser

Closed 2024-02-27.

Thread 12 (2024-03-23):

Bill of materials, beam splitter dimension

ZdenekAster, 2024-03-23:
for actual clamping parts 40x40x5mm for insert to grooves length is approximately 46mm.

PixiePlacer, 2024-04-28:
Can you detail your Comment? I did not understand it ;)

pinballdave, 2024-08-01:
I have just printed the down facing camera housing and clamp for my build, and have seen the same issue.

The BOM lists the glass as 40x40x5mm, the measured dimensions of the 3d printed parts are 48.4 x 41.6mm x 3.7mm.

So is the BOM wrong and a 48x40x3mm glass is needed, or are there other parts required to fit the glass to the down facing camera housing?

Also the drag chain is specified as 50x20mm type, It should be made clear that these are external dimensions, as I mistakenly purchased 50x18mm internal dimension chain (which is 60x23mm external).

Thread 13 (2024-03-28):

Openpnp

ozi1245, 2024-03-28:
Hello my friend, how are you? There is a problem with OpenPnp. Is there a solidworks drawing related to the chassis of the machine?

PixiePlacer, 2024-04-18:
There are Step Filles available for the machine in the repro.

Closed 2024-04-28.

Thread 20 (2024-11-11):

Vaccum Sensing

marcovilla118, 2024-11-11:
Dear All,
what is not clear is where the sensor pressure must be connected to the BTT SKR 1.4? Can some body help me?

Thanks

ThibaudetTevai, 2025-05-08:
I think is not connected !

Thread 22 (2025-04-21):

Dimensions

svetozar161, 2025-04-21:
Hi. I decided to repeat your project and faced the problem of building the frame at the very beginning. You need the dimensions for installing horizontal jumpers. At what height from the base are they screwed? Thank you.

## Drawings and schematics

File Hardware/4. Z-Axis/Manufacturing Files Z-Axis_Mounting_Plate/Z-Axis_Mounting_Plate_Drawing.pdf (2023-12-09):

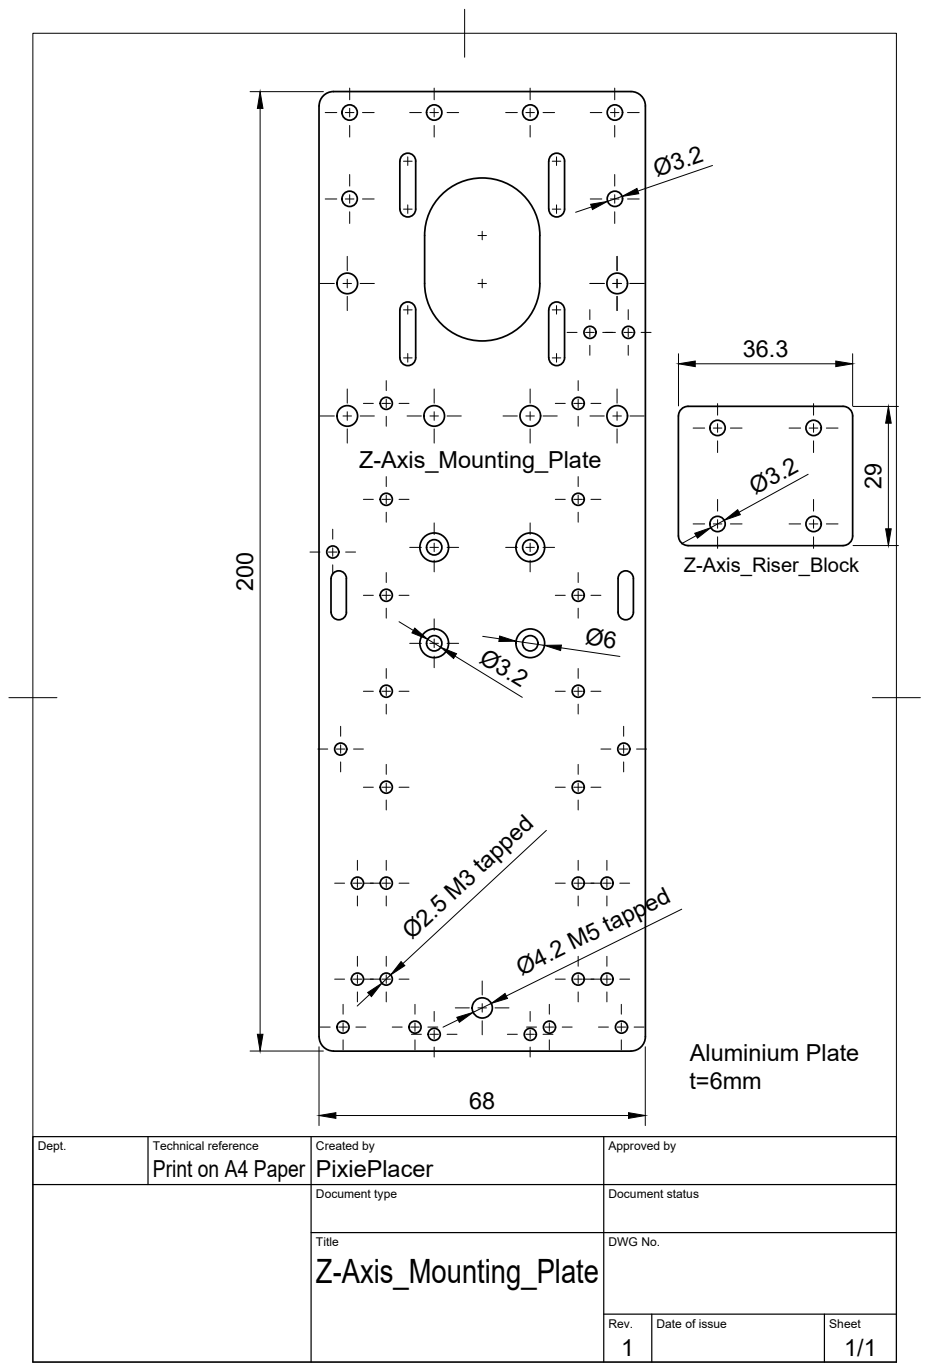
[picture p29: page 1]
Aluminium Plate; Ø2.5 M3 tapped Ø4.2 M5 tapped

Dept. | Technical reference Print on A4 Paper | Created by PixiePlacer | Approved by

Document type | Document status

Title Z-Axis_Mounting_Plate | DWG No.

Rev. 1 | Date of issue | Sheet 1/1

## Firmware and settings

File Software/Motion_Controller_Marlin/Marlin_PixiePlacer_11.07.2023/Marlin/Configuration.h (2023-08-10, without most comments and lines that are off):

#pragma once
#define CONFIGURATION_H_VERSION 02010201
#define STRING_CONFIG_H_AUTHOR "PixiePlacer" // Who made the changes.
#define SHOW_BOOTSCREEN
  #define MOTHERBOARD BOARD_BTT_SKR_V1_4_TURBO
#define SERIAL_PORT -1
#define BAUDRATE 115200
#define SERIAL_PORT_2 0
#define BAUDRATE_2 115200   // :[2400, 9600, 19200, 38400, 57600, 115200, 250000, 500000, 1000000] Enable to override BAUDRATE
#define CUSTOM_MACHINE_NAME "PixiePlacer 11.07.2023"
#define X_DRIVER_TYPE  TMC5160
#define Y_DRIVER_TYPE  TMC5160
#define Z_DRIVER_TYPE  TMC5160
#define E0_DRIVER_TYPE TMC2208
#define E1_DRIVER_TYPE TMC2208
#define EXTRUDERS 2
#define DEFAULT_NOMINAL_FILAMENT_DIA 1.75
#define TEMP_SENSOR_0 998
#define TEMP_SENSOR_1 998
#define TEMP_SENSOR_2 0
#define TEMP_SENSOR_3 0
#define TEMP_SENSOR_4 0
#define TEMP_SENSOR_5 0
#define TEMP_SENSOR_6 0
#define TEMP_SENSOR_7 0
#define TEMP_SENSOR_BED 0
#define TEMP_SENSOR_PROBE 0
#define TEMP_SENSOR_CHAMBER 0
#define TEMP_SENSOR_COOLER 0
#define TEMP_SENSOR_BOARD 0
#define TEMP_SENSOR_REDUNDANT 0
#define DUMMY_THERMISTOR_998_VALUE  25
#define DUMMY_THERMISTOR_999_VALUE 100
#if TEMP_SENSOR_IS_MAX_TC(0)
  #define MAX31865_SENSOR_OHMS_0      100 // (Ω) Typically 100 or 1000 (PT100 or PT1000)
  #define MAX31865_CALIBRATION_OHMS_0 430 // (Ω) Typically 430 for Adafruit PT100; 4300 for Adafruit PT1000
#endif
#if TEMP_SENSOR_IS_MAX_TC(1)
  #define MAX31865_SENSOR_OHMS_1      100
  #define MAX31865_CALIBRATION_OHMS_1 430
#endif
#if TEMP_SENSOR_IS_MAX_TC(2)
  #define MAX31865_SENSOR_OHMS_2      100
  #define MAX31865_CALIBRATION_OHMS_2 430
#endif
#if HAS_E_TEMP_SENSOR
  #define TEMP_RESIDENCY_TIME         10  // (seconds) Time to wait for hotend to "settle" in M109
  #define TEMP_WINDOW                  1  // (°C) Temperature proximity for the "temperature reached" timer
  #define TEMP_HYSTERESIS              3  // (°C) Temperature proximity considered "close enough" to the target
#endif
#if TEMP_SENSOR_BED
  #define TEMP_BED_RESIDENCY_TIME     10  // (seconds) Time to wait for bed to "settle" in M190
  #define TEMP_BED_WINDOW              1  // (°C) Temperature proximity for the "temperature reached" timer
  #define TEMP_BED_HYSTERESIS          3  // (°C) Temperature proximity considered "close enough" to the target
#endif
#if TEMP_SENSOR_CHAMBER
  #define TEMP_CHAMBER_RESIDENCY_TIME 10  // (seconds) Time to wait for chamber to "settle" in M191
  #define TEMP_CHAMBER_WINDOW          1  // (°C) Temperature proximity for the "temperature reached" timer
  #define TEMP_CHAMBER_HYSTERESIS      3  // (°C) Temperature proximity considered "close enough" to the target
#endif
#if TEMP_SENSOR_REDUNDANT
  #define TEMP_SENSOR_REDUNDANT_SOURCE    E1  // The sensor that will provide the redundant reading.
  #define TEMP_SENSOR_REDUNDANT_TARGET    E0  // The sensor that we are providing a redundant reading for.
  #define TEMP_SENSOR_REDUNDANT_MAX_DIFF  10  // (°C) Temperature difference that will trigger a print abort.
#endif
#define HEATER_0_MINTEMP   5
#define HEATER_1_MINTEMP   5
#define HEATER_2_MINTEMP   5
#define HEATER_3_MINTEMP   5
#define HEATER_4_MINTEMP   5
#define HEATER_5_MINTEMP   5
#define HEATER_6_MINTEMP   5
#define HEATER_7_MINTEMP   5
#define BED_MINTEMP        5
#define CHAMBER_MINTEMP    5
#define HEATER_0_MAXTEMP 275
#define HEATER_1_MAXTEMP 275
#define HEATER_2_MAXTEMP 275
#define HEATER_3_MAXTEMP 275
#define HEATER_4_MAXTEMP 275
#define HEATER_5_MAXTEMP 275
#define HEATER_6_MAXTEMP 275
#define HEATER_7_MAXTEMP 275
#define BED_MAXTEMP      150
#define CHAMBER_MAXTEMP  60
#define HOTEND_OVERSHOOT 15   // (°C) Forbid temperatures over MAXTEMP - OVERSHOOT
#define BED_OVERSHOOT    10   // (°C) Forbid temperatures over MAXTEMP - OVERSHOOT
#define COOLER_OVERSHOOT  2   // (°C) Forbid temperatures closer than OVERSHOOT
#define BANG_MAX 255     // Limits current to nozzle while in bang-bang mode; 255=full current
#define PID_MAX BANG_MAX // Limits current to nozzle while PID is active (see PID_FUNCTIONAL_RANGE below); 255=full current
#define PID_K1 0.95      // Smoothing factor within any PID loop
#define MAX_BED_POWER 255 // limits duty cycle to bed; 255=full current
#define MAX_CHAMBER_POWER 255 // limits duty cycle to chamber heater; 255=full current
#define USE_XMIN_PLUG
#define USE_YMIN_PLUG
#define USE_ZMIN_PLUG
#define ENDSTOPPULLUPS
#define X_MIN_ENDSTOP_INVERTING true // Set to true to invert the logic of the endstop.
#define Y_MIN_ENDSTOP_INVERTING true // Set to true to invert the logic of the endstop.
#define Z_MIN_ENDSTOP_INVERTING true // Set to true to invert the logic of the endstop.
#define I_MIN_ENDSTOP_INVERTING false // Set to true to invert the logic of the endstop.
#define J_MIN_ENDSTOP_INVERTING false // Set to true to invert the logic of the endstop.
#define K_MIN_ENDSTOP_INVERTING false // Set to true to invert the logic of the endstop.
#define U_MIN_ENDSTOP_INVERTING false // Set to true to invert the logic of the endstop.
#define V_MIN_ENDSTOP_INVERTING false // Set to true to invert the logic of the endstop.
#define W_MIN_ENDSTOP_INVERTING false // Set to true to invert the logic of the endstop.
#define X_MAX_ENDSTOP_INVERTING true // Set to true to invert the logic of the endstop.
#define Y_MAX_ENDSTOP_INVERTING true // Set to true to invert the logic of the endstop.
#define Z_MAX_ENDSTOP_INVERTING true // Set to true to invert the logic of the endstop.
#define I_MAX_ENDSTOP_INVERTING false // Set to true to invert the logic of the endstop.
#define J_MAX_ENDSTOP_INVERTING false // Set to true to invert the logic of the endstop.
#define K_MAX_ENDSTOP_INVERTING false // Set to true to invert the logic of the endstop.
#define U_MAX_ENDSTOP_INVERTING false // Set to true to invert the logic of the endstop.
#define V_MAX_ENDSTOP_INVERTING false // Set to true to invert the logic of the endstop.
#define W_MAX_ENDSTOP_INVERTING false // Set to true to invert the logic of the endstop.
#define Z_MIN_PROBE_ENDSTOP_INVERTING true // Set to true to invert the logic of the probe.
#define DEFAULT_AXIS_STEPS_PER_UNIT   { 80, 80, 80, 8.888}
#define DEFAULT_MAX_FEEDRATE          { 200, 120, 100000,  1000}
#define DEFAULT_MAX_ACCELERATION      { 500, 500, 3000, 1000}
#define DEFAULT_ACCELERATION          3000    // X, Y, Z and E acceleration for printing moves
#define DEFAULT_RETRACT_ACCELERATION  3000    // E acceleration for retracts
#define DEFAULT_TRAVEL_ACCELERATION   3000    // X, Y, Z acceleration for travel (non printing) moves
#define CLASSIC_JERK
  #define DEFAULT_XJERK 0.0
  #define DEFAULT_YJERK 0.0
  #define DEFAULT_ZJERK 0.0
#define DEFAULT_EJERK    0  // May be used by Linear Advance
#define NOZZLE_TO_PROBE_OFFSET { 0, 0, 0 }
#define PROBING_MARGIN 100
#define XY_PROBE_FEEDRATE 50
#define Z_PROBE_FEEDRATE_FAST 50
#define Z_PROBE_FEEDRATE_SLOW 10
#define MULTIPLE_PROBING 2
#define Z_CLEARANCE_DEPLOY_PROBE   10 // Z Clearance for Deploy/Stow
#define Z_CLEARANCE_BETWEEN_PROBES  5 // Z Clearance between probe points
#define Z_CLEARANCE_MULTI_PROBE     5 // Z Clearance between multiple probes
#define Z_PROBE_LOW_POINT          -83 // Farthest distance below the trigger-point to go before stopping
#define Z_PROBE_OFFSET_RANGE_MIN -82
#define Z_PROBE_OFFSET_RANGE_MAX 160
#define X_ENABLE_ON 0
#define Y_ENABLE_ON 0
#define Z_ENABLE_ON 0
#define E_ENABLE_ON 0 // For all extruders
#define DISABLE_X false
#define DISABLE_Y false
#define DISABLE_Z false
#define INVERT_X_DIR true
#define INVERT_Y_DIR true
#define INVERT_Z_DIR true
#define INVERT_E0_DIR false
#define INVERT_E1_DIR false
#define INVERT_E2_DIR false
#define INVERT_E3_DIR false
#define INVERT_E4_DIR false
#define INVERT_E5_DIR false
#define INVERT_E6_DIR false
#define INVERT_E7_DIR false
#define X_HOME_DIR -1
#define Y_HOME_DIR -1
#define Z_HOME_DIR -1
#define X_BED_SIZE 610
#define Y_BED_SIZE 529
#define X_MIN_POS 0
#define Y_MIN_POS 0
#define Z_MIN_POS 0
#define X_MAX_POS X_BED_SIZE
#define Y_MAX_POS Y_BED_SIZE
#define Z_MAX_POS 200
#define MIN_SOFTWARE_ENDSTOPS
  #define MIN_SOFTWARE_ENDSTOP_X
  #define MIN_SOFTWARE_ENDSTOP_Y
  #define MIN_SOFTWARE_ENDSTOP_I
  #define MIN_SOFTWARE_ENDSTOP_J
  #define MIN_SOFTWARE_ENDSTOP_K
  #define MIN_SOFTWARE_ENDSTOP_U
  #define MIN_SOFTWARE_ENDSTOP_V
  #define MIN_SOFTWARE_ENDSTOP_W
#define MAX_SOFTWARE_ENDSTOPS
  #define MAX_SOFTWARE_ENDSTOP_X
  #define MAX_SOFTWARE_ENDSTOP_Y
  #define MAX_SOFTWARE_ENDSTOP_I
  #define MAX_SOFTWARE_ENDSTOP_J
  #define MAX_SOFTWARE_ENDSTOP_K
  #define MAX_SOFTWARE_ENDSTOP_U
  #define MAX_SOFTWARE_ENDSTOP_V
  #define MAX_SOFTWARE_ENDSTOP_W
#define HOMING_FEEDRATE_MM_M { 4000, 4000, 4000 }
#define VALIDATE_HOMING_ENDSTOPS
#define EEPROM_SETTINGS     // Persistent storage with M500 and M501
#define EEPROM_CHITCHAT       // Give feedback on EEPROM commands. Disable to save PROGMEM.
#define EEPROM_BOOT_SILENT    // Keep M503 quiet and only give errors during first load
#define HOST_KEEPALIVE_FEATURE        // Disable this if your host doesn't like keepalive messages
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

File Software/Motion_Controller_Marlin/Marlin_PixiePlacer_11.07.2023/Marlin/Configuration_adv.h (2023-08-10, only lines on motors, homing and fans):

#define E0_AUTO_FAN_PIN -1
#define E1_AUTO_FAN_PIN -1
#define E2_AUTO_FAN_PIN -1
#define E3_AUTO_FAN_PIN -1
#define E4_AUTO_FAN_PIN -1
#define E5_AUTO_FAN_PIN -1
#define E6_AUTO_FAN_PIN -1
#define E7_AUTO_FAN_PIN -1
#define CHAMBER_AUTO_FAN_PIN -1
#define COOLER_AUTO_FAN_PIN -1
#define HOMING_BUMP_MM      { 0, 0, 2 }       // (linear=mm, rotational=°) Backoff from endstops after first bump
#define HOMING_BUMP_DIVISOR { 2, 2, 4 }       // Re-Bump Speed Divisor (Divides the Homing Feedrate)
#define MICROSTEP_MODES { 16, 16, 16, 16, 16, 16 } // [1,2,4,8,16]
    #define X_CURRENT       1500        // (mA) RMS current. Multiply by 1.414 for peak current.
    #define X_CURRENT_HOME  X_CURRENT  // (mA) RMS current for sensorless homing
    #define X_MICROSTEPS     16        // 0..256
    #define Y_CURRENT       1500
    #define Y_CURRENT_HOME  Y_CURRENT
    #define Y_MICROSTEPS     16
    #define Z_CURRENT       1500
    #define Z_CURRENT_HOME  Z_CURRENT
    #define Z_MICROSTEPS     16
    #define E0_CURRENT      600
    #define E0_MICROSTEPS    16
    #define E1_CURRENT      600
    #define E1_MICROSTEPS   E0_MICROSTEPS
    #define CURRENT_STEP_DOWN     50  // [mA]
    #define REPORT_CURRENT_CHANGE
  #define X_HYBRID_THRESHOLD     100  // [mm/s]
  #define X2_HYBRID_THRESHOLD    100
  #define Y_HYBRID_THRESHOLD     100
  #define Y2_HYBRID_THRESHOLD    100
  #define Z_HYBRID_THRESHOLD       3
  #define Z2_HYBRID_THRESHOLD      3
  #define Z3_HYBRID_THRESHOLD      3
  #define Z4_HYBRID_THRESHOLD      3
  #define I_HYBRID_THRESHOLD       3  // [linear=mm/s, rotational=°/s]
  #define J_HYBRID_THRESHOLD       3  // [linear=mm/s, rotational=°/s]
  #define K_HYBRID_THRESHOLD       3  // [linear=mm/s, rotational=°/s]
  #define U_HYBRID_THRESHOLD       3  // [mm/s]
  #define V_HYBRID_THRESHOLD       3
  #define W_HYBRID_THRESHOLD       3
  #define E0_HYBRID_THRESHOLD     30
  #define E1_HYBRID_THRESHOLD     30
  #define E2_HYBRID_THRESHOLD     30
  #define E3_HYBRID_THRESHOLD     30
  #define E4_HYBRID_THRESHOLD     30
  #define E5_HYBRID_THRESHOLD     30
  #define E6_HYBRID_THRESHOLD     30
  #define E7_HYBRID_THRESHOLD     30
  #define SENSORLESS_HOMING // StallGuard capable drivers only
    #define X_STALL_SENSITIVITY  5
    #define X2_STALL_SENSITIVITY X_STALL_SENSITIVITY
    #define Y_STALL_SENSITIVITY  7
    #define Y2_STALL_SENSITIVITY Y_STALL_SENSITIVITY

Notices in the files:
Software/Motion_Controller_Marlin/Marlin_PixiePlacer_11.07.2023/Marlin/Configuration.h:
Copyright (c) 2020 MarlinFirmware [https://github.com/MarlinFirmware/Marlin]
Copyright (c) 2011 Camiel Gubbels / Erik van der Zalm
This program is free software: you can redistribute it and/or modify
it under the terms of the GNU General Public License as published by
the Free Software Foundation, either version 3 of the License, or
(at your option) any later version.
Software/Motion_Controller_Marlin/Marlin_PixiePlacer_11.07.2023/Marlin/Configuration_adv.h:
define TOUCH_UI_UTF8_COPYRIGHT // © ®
